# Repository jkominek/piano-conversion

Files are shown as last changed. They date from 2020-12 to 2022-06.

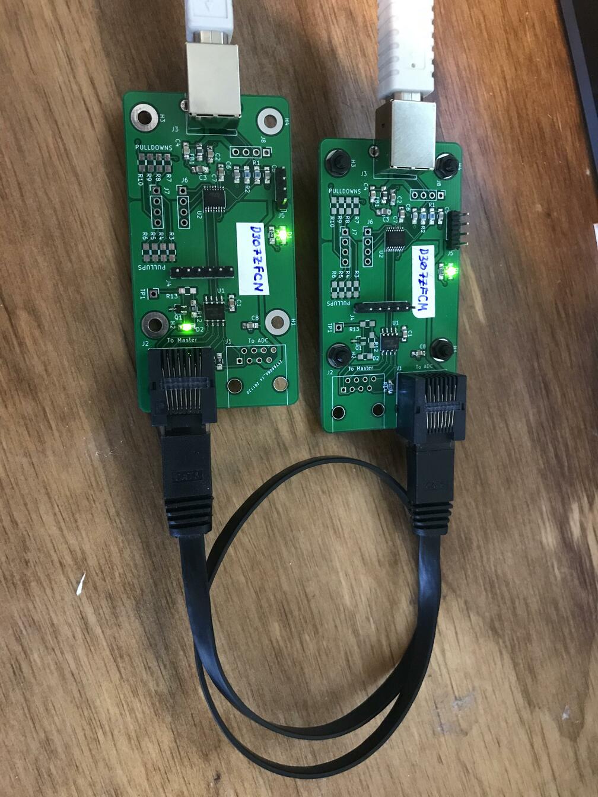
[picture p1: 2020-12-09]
images/link_adapters.jpg

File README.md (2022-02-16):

# About

This represents work on hardware/software for converting acoustic
pianos in to full featured MIDI controllers. The idea is to take
untunable pianos, or pianos whose restoration cost would wildly
exceed their value, and make something useful out of them.

See [the FAQ](https://github.com/jkominek/piano-conversion/wiki/FAQ)
to have common / likely questions answered.

Later work may expand that scope.

It was inspired by Evgeni Kumanov (CyberGene)'s "Cybrid" controller:
https://github.com/ekumanov/cybrid/

# Warning!

The hardware designs are unfinished. Some have not been fabricated.
Most have barely been tested, and there is not firmware to run a
completed system.

See the [Status page](https://github.com/jkominek/piano-conversion/wiki/Status) for where things stand.

# A Very Brief Overview

* hardware
  * Where most of the work has taken place. KiCad schematics and board
    layouts for the system.
* cubemx
  * STCubeMX files which correspond to the boards, the idea being that
    if you want to write your own firmware, you can start from here,
    and know that your pin assignments and such are all sane.
* firmware
  * Board firmware, some other stuff
* analyses
  * Data collected, and code/notes for processing it.
* mechanical
  * OpenSCAD files for physical parts which have been useful in
    construction of my prototype.

# More

See [DESIGN.md](https://github.com/jkominek/piano-conversion/blob/master/DESIGN.md) for system design information.

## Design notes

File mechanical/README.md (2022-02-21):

# Mechanical parts

Mechanical design is wholly outside the scope of this project.

There's too much variability in piano design, and personal aesthetics, for
a single mechanical design to be a productive goal.

But it can't hurt to put in some of the materials I've used. Most of them
will be OpenSCAD files, as the parts are simple, and OpenSCAD is available
to everyone. They might give you some ideas.

* odd_supports
  * Lets you make very complicated mounts to hold a dual slot 4040 extrusion up in the air at arbitrary angles, using two 2020 supports.
* cny70-protector
  * A plate to put over the CNY70 PCBs, which leaves the sensors exposed, while protecting them from direct hammer strikes.
* back-block & lr-block
  * Some simple blocks intended to mount onto single slot 4040 extrusions and hold the keybed from the side.
* mounting_plate
  * Adapter which holds my larger PCBs to the dual-slot 4040 extrusions.

More stuff will be forth coming.

# Sources of useful things

* Amazon is full of cheap hardware.
* McMaster-Carr, if you're not aware of it, will sell you just about every mechanical widget there is, for the right place.
* Misumi is my preferred supplier for aluminum extrusions. They'll cut and customize them for very reasonable prices, and are very precise.

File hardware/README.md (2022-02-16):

# What's in here

* adc-board
  * An STM32H743 reading 22 ADC channels and sending the results over RS485.
* led-power
  * Provides power to 8 strings of 22 CNY70 IR LEDs. Needs +48V. Optional I2C control.
* led-test-bar
  * For development only: little bar that holds a bunch of LEDs for testing the LED power board.
* link-adapter
  * For development only: allows a PC to connect to an ADC or main board.
* main-board
  * 8 ADC boards can plug in, their processed signals are managed
    by another STM32H743 and converted to MIDI in its various forms.
    Intended mainly for USB use, also has ethernet designed in.
    For all of the optional accessories, there are three I2C ports in
    the form of Qwiic connectors, for plugging in MIDI & pedal boards,
    and whatever other craziness you can conjure up.
* midi-board
  * An I2C to MIDI DIN board. Gets the extra UART, optos and DIN
    connectors off the main board so they're not taking up space if
    you don't need them.
* pedal-board
  * 4 1/4" TRS jacks for common MIDI keyboard pedals. STM32G0 for reading
    the signals and making them available to the main board via I2C.
* sensorboard-tester
  * For development/manufacture only, for testing/measuring sensorboards/CNY70s.
* sensorboards
  * Directory with a variety of board configurations for holding CNY70 sensors.

To put a sensor on every hammer and key of an 88 key piano, you would need:

* 176 sensor boards
* 8 ADC boards
* 1 main board
* 1 LED power board

Everything else is optional, but might make your life better.

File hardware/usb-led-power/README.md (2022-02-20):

This is a little USB-powered board which produces 4 constant current
outputs, each fixed to 20mA. Max voltage is 24V. With an LED Vf of
1.5V, that means you can drive <=16-ish LEDs off of each output. If
you drive just a single LED off an output, the constant current
limiter will be shedding 0.45W. It can probably handle that, but if
you want to use an output with fewer than 8 LEDs, consider putting a
resistor in series with them.  Remember V=IR. I is 20mA. Choose R to
eat 50-75% of whatever voltage will be left over after you subtract
the forward voltages of the LEDs from 24V.

The outputs inherit rather more noise from the USB power supply than I
would like. Which justifies much of the hassle I went through with the
design of the real LED power board. But if you don't like that one, or
want something for testing purposs, this might be helpful.

I don't generally suggest using it.

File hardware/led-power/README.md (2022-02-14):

# LED Power board

As covered in the main design doc, the board takes +48V, and uses them
to feed 8 strings of LEDs with a constant current of ~20mA.

# Design

See [the wiki page about the board](https://github.com/jkominek/piano-conversion/wiki/LED-Power-Board) for details on how it works.

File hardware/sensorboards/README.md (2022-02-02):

What do we have here?

* simple-1x
  * A single sensor board that tries to be generically useful
* 2040-centered-1x
  * A single sensor board that centers the sensor across the 40mm wide portion of a 20x40mm tslot aluminum extrusion.
* 2040-centered-2x
  * Same thing, but two sensors on one board.
* 2040-centered-4x
  * Same thing, but four sensors on one board.
* 2040-centered-4x-12deg
  * Same thing, but four sensors on one board and they're rotated 12 degrees, for bass hammers.
* 2020-offset-1x
  * A single sensor board that places the sensor to one side of a 20x20mm extrusion, and the connector on the other side.
* 2020-offset-2x
  * Same thing, but two sensors on one board.
* 2020-offset-4x
  * Same thing, but four sensors on one board.

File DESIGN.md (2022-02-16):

# Requirements / Goals

* Semiautomated calibration. Ideally once the hardware is correctly
  installed, it can be calibrated by playing all of the notes in
  order. It is expected this will require an attached PC running
  specialized software.
* It must be possible to make this work with just the extracted action
  of a grand piano. Mechanics are outside of the scope of what this
  project intends to worry about, but it would be ideal if a MIDI
  controller housing could be made for a piano's action, such that the
  action could be transferred between controller housing and piano
  with ease.
* Support for multiple common 1/4" TRS sustain pedals, or some other
  sensors that would be suitable for measuring the state of pedals
  still in their original state.
* The boards should be designed such that bad firmware can't wreck
  anything. I feel like this is important for open hardware type projects,
  where there is the possibility that folks might start fiddling
  with their firmware without a full understanding of the hardware.

### Distant future goals

* Integration with a Raspberry Pi 4 Compute Module capable of running
  Pianoteq so that a standalone piano can be produced.
* Alternatively, try to figure out how to get some open source synth
  software running on some sort of microcontroller, such that it can
  take MIDI over I2C and generate audio.
* Design/integration of DACs and audio amplifiers into that synth board,
  so that it can drive speakers directly.

# System Design

The hardware/software system is based around the Vishay
[CNY70](https://github.com/jkominek/piano-conversion/wiki/CNY70)
optical reflectance sensor. It consists of an infrared LED, and a
phototransistor sensitive to the LED, in a convenient package. It can
measure distances in the (roughly!) 0-10mm range.

In the full version of this conversion, 88 of those sensors would be
placed under the keys to detect note-off time & velocity, and 88 of them
placed at the end of the hammers' travel, so as to measure note-on timing
and velocity. This would prevent the "loud note" problem that troubles
some hybrid pianos. Additionally, information from the key sensors may be
used to signal to the synthesizer that the damper has been raised
(permitting resonsnace) before the hammer strikes. Sample based synths
could also use that information to preload samples.

(During the initial design of this I completely forgot that pianos usually
don't dampen the highest strings. If you want to leave the top 22 notes
undampened, you could eliminate one of the ADC boards. Or you could convert
a >88 key piano.)

### ADC Board

That's 176 sensors in a piano. 22 are monitored by each of these
boards.  The current through each one is converted to a voltage by a
transimpedance amplifier, and monitored by an ADC channel of an
[STM32H743](https://github.com/jkominek/piano-conversion/wiki/STM32H7).
Hopefully the STM32 will be able to process all 22 signals at between
10kHz and 20kHz. I expect to apply some digital low pass filtering.

Once the processor has determined that a note on, or off, is occurring
and measured the velocity, it is sent out over a RS485 serial
link. Use of RS485 should allow us to spread these boards out through
the structure of the controller, while maintaining relatively high
speed serial communications. The RS485 link takes place over two
twisted pairs of an ethernet cable. (NOTE we are NOT using ethernet,
just taking advantage of the large supply of high quality premade
cabling and jacks.) Having two twisted pairs permits full duplex
communication.

The same cable also carries ~5V power. Each board includes a single
switching regulator to bring the 5V down to 3.3V. The analog voltage
rails are produced by linear regulators, to reduce noise.

The board can be populated with optional components to make it into
a USB device. This isn't expected to be necessary, but may be more
convenient during the sensor calibration process. Two additional UARTs
are brought out to 0.100" header pins. Just in case.

Programming is performed over the JTAG header, intended for use with the
ST-Link/v2 programmer.

There is space for four LEDs, and a number of otherwise-unused pins are
brought out to sizable test points.

### Sensor board

Each sensor board will consist of nothing but some CNY70s, and a
0.100" header. 2*N pins will connect to the phototransistors, and come
back to the ADC board via twisted pair. The last two correspond to a
chain of all of the LEDs on the board.  The LEDs should be chained
together in rather long strings. Likely 22 sensors per string.

### LED power board

The LED power board is designed (as of rev3) to use an off the shelf
48V power supply, and provide a constant ~20mA to 8 different strings
of LEDs. Each string is intended to have 22 CNY70 LEDs on it.

We derive from the 48V a ~12V power rail for the rest of the analog
electronics on the board. The design as it stands should produce
constant currents which are extremely stable from time scales of a
year, down to 100kHz. The deterioration of the LEDs themselves is
expected to be the main source of change in the optical output.

Rev3 of the board adds a microcontroller which can monitor the LED
strings individually to detect errors, and also turn all the LEDs off
by shutting down the precision voltage reference.

### Main board

Intended to use a STM32H743 like the ADC board.

8 RS485 serial links, along with 5V distribution to the ADC boards.
Per-board high-side MOSFET control of power, so that boards
can be brought up in sequence once power has stabilized. Also allows
them to be power cycled in event of error, or to reflash them.

USB B device link, as the main/intended link to the host computer.

Four I2C controllers are brought out to three separate Qwiic headers,
so that a variety of common I/O devices can be attached without
requiring special development. (MIDI DIN, pedals, led power control,
RTC clock, ethernet/bluetooth, blinky RGB LEDs, etc)

Firmware is expected to process the fairly raw velocity messages
from the ADC boards, appyling any calibration, and sending them out
over any of the many MIDI links available to it (serial, USB, ethernet,
maybe even bluetooth).

#### Pedal board

A low powered STM32G0 a board with Qwiic headers, and 4 1/4"
TRS jacks for standard sustain pedals. 12 ADC channels go to
every pin of the TRS jacks in hopes that we can automatically
determine the behavior of the attached pdals.

#### MIDI board

Like the pedal board, the MIDI board is designed as a Qwiic device.
It also uses an STM32G0 to act as an I2C<->UART bridge, and has the
appropriate MIDI isolation circuitry.

### Link board

To facilitate development/testing of the ADC boards without the main
board, a "link board" has been designed. It is a full duplex RS485
board with power injection comparable to what the main board will
provide.

As an alternative to using the main board, a PC with enough link
boards to talk to all of the ADC boards simultaneously could skip out
on the use of a main board, in exchange for running more complicated
software locally.

# Construction/assembly requirements

See [the wiki Assembly Notes](https://github.com/jkominek/piano-conversion/wiki/Assembly-Notes)
for this info.

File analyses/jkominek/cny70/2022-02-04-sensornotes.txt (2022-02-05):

Put a CNY70 on a motorized stage, aimed at a white surface.
Moved it around, linearly, then at random, taking measurements
of the output. Phototransistor was fed into a TIA. High voltage
on the PT was 3.2584V. Reference voltage on the opamp was 1.9799V.
So there was 1.2749V across the phototransistor.

Voltages were measured with a EEVBlog 121GW multimeter.
Motion provided by a Creality Ender 3 V2.
Distances confirmed with Mitutoyo CD-6" ASX digital calipers.

poscommanded,posmeasured
5,4.66
10,9.66
15,14.66
20,19.57

All millimeters. Looks like the first column of the data needs -0.33
applied.  I think I was smashing the sensor into the target by 0.33mm.
Explains why it goes flat <=0.33

Maximum possible value for the raw data is ~1.9799V.

Gnuplot command for reasonable plot is

plot [0:] "2022-02-04-sensorlog.txt" using ($1-0.33):(1.9799-$2) with point

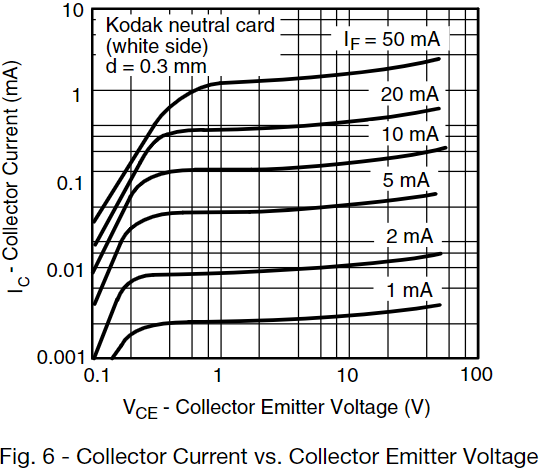
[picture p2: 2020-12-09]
images/ic_vs_vce.png

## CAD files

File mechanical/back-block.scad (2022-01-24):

rotate([180,0,0])
difference() {
  union() {
    cube([40, 50, 10]);
    translate([15, 0, -2]) {
      cube([10, 50, 2]);
    }
  }
  translate([20,10,-2.1]) {
    cylinder(h=14, d=5.2, $fn=32);
  }
  translate([20,40,-2.1]) {
    cylinder(h=14, d=5.2, $fn=32);
  }
}

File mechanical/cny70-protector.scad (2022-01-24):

xy = 7.5;
width = 9;
length = xy+(2.5+0.2)*2;
sensor_height = 5.6;
sensor_gap = 2;
// left to right, l_hammer_size > r_hammer_size
l_hammer_size = 33.5;
r_hammer_size = 33.3;
l_curvature = l_hammer_size / 2;
r_curvature = r_hammer_size / 2;

curvature_x0 = l_curvature;
curvature_m = (r_curvature - l_curvature) / 3;

module cny70_gap() {
  minkowski() {
    cube([xy, xy, (sensor_height+sensor_gap)*1.5]);  
    cylinder(h=0.1, r=0.2);
  }
}

module multiprotect(x) {
 imax = x-1;
 difference() {
   translate([0, -11.25, 0])
     cube([12.5*imax+xy,
           30,
           (sensor_height + sensor_gap)]);

   for(i=[0:imax]) {
      translate([i*12.5, 0, 0])
        #cny70_gap();
   }
   /*
   translate([0, xy/2, 0])
     for(i=[0:imax]) {
       curvature = curvature_x0 + curvature_m * i;
       translate([12.5*i, 0, curvature+sensor_height+sensor_gap])
         rotate([0, 90, 0])
           cylinder(h=12.5, r=curvature);
     }
   */
   translate([0, xy/2, 0])
     for(y=[-1:2:1]) {
       for(i=[0:(imax-1)]) {
         translate([10+12.5*i, y*-10, 2])
           cylinder(h=30, d=6.5, $fn=19);
         translate([10+12.5*i, y*-10, -2])
           cylinder(h=4, d=4.1, $fn=9);
       }
     }
  /*
  translate([0, -sensor_height/2, sensor_height/2])
    #sphere(r=2);
  */
 }
}

multiprotect(4);

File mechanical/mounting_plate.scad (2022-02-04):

x=1;

difference() {
    union() {
        minkowski() {
          translate([45, 0, 0])
            cube([25, 3*25.4, 5], center=true);
          cylinder(h=0.1, r=5);
        }
        for(y=[-1:2:1]) {
            translate([x*1.5*25.4, y*1.5*25.4, 0])
              cylinder(h=5, d=8);
        }
    }
    
    for(y=[-1:2:1]) {
        translate([x*1.5*25.4, y*1.5*25.4, 0])
          cylinder(h=20, d=3.5, center=true);
        
        translate([x*55, y*10, 0])
          cylinder(h=20, d=6, center=true);
    }
}

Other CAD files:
mechanical/lr-block.scad
mechanical/odd_supports.scad

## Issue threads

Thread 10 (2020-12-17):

LED Power Rev 1

jkominek, 2020-12-17:
Most of the fixes necessary for Rev 1 have been made and are covered under the [Board Revision Notes](https://github.com/jkominek/piano-conversion/wiki/Board-Revision-Notes).

- [x] Ferrite beads on the incoming power lines? The +15V and +48V are only used by linear devices, so the only HF noise will come from the supplies. We're not generating anything we should try to trap.
- [x] Final schematic/footprint/layout check.

jkominek, 2020-12-20:
78025ad didn't bother putting ferrites on here, The digital logic is optional, and even when present will only be used occasionally to check that the LED strings are still active. I did make the I2C address configurable, though. Jumpers or SMT resistors, as I did on all the other boards.

Closed 2020-12-20.

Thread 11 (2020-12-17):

Link adapter Rev 1

jkominek, 2020-12-17:
All the desired fixes/changes have been made. I don't anticipate bringing these up, they're just cheap enough they're worth getting in case I need more adapters; no sense building the old design.

- [x] Final schematic/footprint/layout check.

jkominek, 2020-12-20:
made some silkscreen improvements in 156ddb7. also improved a few net names making it easier to read the layout.

Closed 2020-12-20.

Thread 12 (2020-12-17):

MIDI board Rev 0

jkominek, 2020-12-17:
- [x] Might be able to drop one of the logic buffers, since we've moved the UART right onto the board. Check that. Want to keep the open collector inverter, as it means we don't have to configure the UART to invert bits or anything for us.
- [x] FInal schematic/footprint/layout check.

jkominek, 2020-12-18:
1d04dc2 removes the extra buffer, finishes the incomplete reset net, and tidies up some layout.

Closed 2020-12-18.

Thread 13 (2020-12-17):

Pedal board Rev 0

jkominek, 2020-12-17:
- [x] Final schematic/footprint/layout check.

jkominek, 2020-12-18:
fecdb71 splits the analog/digital power rails (more or less), and adds a second Qwiic header.

Closed 2020-12-18.

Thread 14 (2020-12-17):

LED Power Rev 1 bringup

jkominek, 2020-12-17:
- [x] Make sure the 5V regulator doesn't explode the MCP1501.
- [x] Check IO expander. Not necessary for a useful board.
- [x] Check I2C pass through performance?

jkominek, 2021-01-04:
IO expander can control the voltage reference, but reading back the status of the lines seems a little off. Probably because all the pins are floating. Will need to finish populating all of the resistors in the middle and check that again.

jkominek, 2021-01-05:
IO expander is fine. It occurs to me that it can check whether or not the individual lines are on, but it can't tell if the 15V and 48V are live. Should add some voltage dividers and hook those up to some more of the IO expander pins.

jkominek, 2021-01-05:
I2C passthrough seems fine

Closed 2021-01-05.

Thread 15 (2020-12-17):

ADC Board Rev 1 bringup

jkominek, 2020-12-17:
- [x] Check adjusted power supply filtration.
- [x] Check MCP120 chip.
- [x] Check 2V regulator.
- [x] Check transimpedance amplifiers.
- [x] Check JTAG header works right now.
- [x] Check RS485 wiring
- [x] Should put a microcontroller on to ensure that some of the rearranged digital lines are ok (the UART in particular)

We'll want the new TIA circuits for testing/writing analog processing code going forward.

jkominek, 2021-01-06:
Hmm not sure what I meant by "adjusted power supply filtration". Using surface mount caps? Guess I can compare old & new +3.3V lines on the scope.

jkominek, 2021-01-13:
+5V and +3.3V looked pristine when I was checking the MCP120 at power-on. Calling that good enough.

jkominek, 2021-01-14:
UART3 to RS485 works fine.

Closed 2021-01-14.

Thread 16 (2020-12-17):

Minor boards

jkominek, 2020-12-17:
- [x] Sensorboard, final schematic/footprint/layout check.
- [x] Sensorboard tester, final schematic/footprint/layout check.
- [x] LED test bar, final schematic/footprint/layout check.

jkominek, 2020-12-18:
LED test bar: Added copper pours for the lowest voltage net on the board, some corresponding large exposed pads for clipping onto, and silk screen for them.

jkominek, 2020-12-20:
bfe854e Sensorboard: finally looked at the gerber files for the Cybrid sensor, and better matched their dimensions. Got the width down to 9mm, and moved the sensor 10mm from the mounting hole center. I wouldn't be surprised if different pianos end up needing a variety of different boards, (Including ideally some boards that hold multiple sensors.) But this should serve as a better starting place.

jkominek, 2020-12-20:
6f696a1 Sensorboard tester: while working on the sensorboard, realized that the header on it might need to be installed backwards, to ensure clearance for hammers striking the sensor, or whatever. So I added mirrored female receptacles on the tester board, to allow for plugging in reversed sensorboards.

Closed 2020-12-20.

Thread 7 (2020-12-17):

ADC Board Rev 0 bring up

jkominek, 2020-12-17:
There are three bring up issues to check before the Rev 1 schematic can be finalized:

- [x] Test that the USART/RS485 transceiver work correctly. It _should_ be fine, as I used the same symbol/footprint as the link adapter board, and USARTs are simple, but... who knows.
- [x] Test that the 22 channels of near-simultaneous ADC conversion works. I should really have done this sooner, as the project relies heavily on this working.
- [x] See if the built-in bootloader works on initial power up. The ST app note on the bootloader has some ominous warnings about V9 of the bootloader, which is the most recent, and presumably what I've got on my parts.
- [x] Slightly easier, see if it works on the USART pins we're currently using. Moving to a different USART probably isn't a problem, but why mess with a layout that seems ok.

jkominek, 2020-12-17:
Z/Y pins on the RS485 transceiver were swapped. Schematic and layout have been fixed (not yet committed).

jkominek, 2020-12-18:
Bootloader seems to be responsive on USART3 immediately after power on, no shenanigans required. I'm not quite getting it to do what I want, but "responsive" is all I can hope for from a hardware standpoint. c76639c swaps USART1 and USART3 on the RS485 transceiver.

jkominek, 2020-12-20:
22 channels of ADC conversion at 15kHz seems to work ok. Not sure about the conversion noise, but I'm pretty sure there is a lot of room for tweaking once I'm taking data off of real sensors watching real hammers/keys. So... design looks workable!

Closed 2020-12-20.

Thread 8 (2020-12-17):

ADC Board Rev 1

jkominek, 2020-12-17:
Most of the fixes necessary for Rev 1 have been made and are covered under the [Board Revision Notes](https://github.com/jkominek/piano-conversion/wiki/Board-Revision-Notes).

- [x] Completion of #7
- [x] Bring out MCO1 and MCO2 on some test points, or at least confirm that the existing test points expose some timer pins. Goal is to make it convenient to measure the frequency stability of the built-in oscillators,
- [x] Triple check the transimpedance amplifier design in the analog half. @DigitalExegete agreed to help. :)
- [x] Final symbol/footprint/layout checks.

jkominek, 2020-12-20:
Past me was a genius, MCO1 and MCO2 are already available on test points. The same pins (PA8/TP26, PC9/TP25) also have some timer outputs on them.

jkominek, 2020-12-21:
c9634bf tweaked the edges of some of the copper pours around the analog area, and adjusted the routing on the NRST line.

jkominek, 2020-12-21:
been staring at the TIA forever. pretty sure we're good to go.

Closed 2020-12-21.

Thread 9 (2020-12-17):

Main Board Rev 0

jkominek, 2020-12-17:
Subtasks:

- [x] Triple check the high-side power control of ADC boards.
- [x] Include a SPI memory part, EEPROM or FLASH, or something. Find a common footprint, we can worry about what size memory (or even if we'll use it) later.
- [x] Double check the UART pin assignments, make sure we don't have an RS485 transceiver hooked up to something that isn't a UART.
- [x] Final symbol/footprint/layout check. Don't forget ERC/DRC.

jkominek, 2020-12-21:
63abe29 Fixes a UART pin error, _and_ an I2C pin error. Sigh.

jkominek, 2020-12-21:
0f9a079 includes an SPI flash using a common footprint for a SPI memory.

jkominek, 2020-12-21:
5072ae0 Must've been in a hurry when I did the power control. Had the p-channel FETs backwards. And an extra resistor on each one that I can't, for the life of me, figure out why I wanted. FETs flipped, resistor removed, and package layout made pleasingly symmetric.

jkominek, 2020-12-21:
016cd60 ran ERC/DRC, removed some unused nets and marked the pins NC. (leftovers from when I thought the pedal inputs might come to this board directly.)

jkominek, 2020-12-21:
Pretty sure we're all done with this. 3a703c3 moved the ethernet LEDs to a single 2x3 header. A 1x3 is still used for boot selection, but I'd expect most users to jumper that. I'm expecting this will need another rev, so I'll worry about putting in pads to allow it to be set during surface mount assembly in that rev.

Closed 2020-12-21.

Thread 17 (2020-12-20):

Update PCB layouts with new revision number & generate gerber files

jkominek, 2020-12-20:
I update the board revision number right before producing gerber files. So this will be the very last thing to do on the milestone.

- [x] Commit updated silkscreen for all boards

Generate gerber files for the following, and attach to the release:

- [x] Main board
- [x] ADC board
- [x] LED power
- [x] LED test
- [x] Sensor board
- [x] Sensor test
- [x] Pedal
- [x] MIDI
- [x] Link adapter

jkominek, 2020-12-22:
gerber zips generated, and attached to release.

Closed 2020-12-22.

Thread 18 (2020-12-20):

Main board rev 0 bringup

jkominek, 2020-12-20:
- [ ] ~~Qwiic header pass-through~~ Every one on the main board is its own bus, this item must've predated that change.
- [x] Power input, reverse polarity protection & regulation
- [x] Control of N/P channel MOSFET array
- [x] 20MHz ~~& 25MHz~~ oscillators
- [x] One stack of RS485 transceiver & jacks, to confirm correct wiring (sigh)
- [x] Microcontroller (UARTs & I2C primarily)
- [ ] ~~Ethernet chip, magjack, and microcontroller use of ethernet~~ Going to move networking onto an optional board.

jkominek, 2021-01-03:
tempted to move the ethernet off this board in the next rev, in which case i probably wouldn't bother to bring it up on here.

jkominek, 2021-01-09:
JTAG works and the STM32 is still live after my hand soldering. I'll have to cobble together some firmware to test the UART and I2C.

jkominek, 2021-01-14:
brought the stcubemx project definition up to date. should be good to generate a basic project and start poking things.

jkominek, 2021-01-15:
USB D+/D- are swapped.

jkominek, 2021-01-15:
UART4 and USB are fine.

jkominek, 2021-01-15:
and I2C4 works, so we're all set i think.

Closed 2021-01-15.

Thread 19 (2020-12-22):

Pedal board Rev0 bringup

jkominek, 2020-12-22:
- [x] Assembly
- [x] Check that the ADS7830 works
- [ ] Check it with a pedal

jkominek, 2021-01-20:
didn't really get the pedal pinout right enough to be worth trying it with a pedal. ehhh.

Closed 2021-01-20.

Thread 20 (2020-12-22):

MIDI Board Rev0 bring up

jkominek, 2020-12-22:
- [x] Assembly
- [x] Check MIDI out circuitry
- [x] Check MIDI in circuitry
- [x] Check the SC16IS741

jkominek, 2021-01-02:
UART is functional. rev0 appears to have no errors that prevent its use.

Closed 2021-01-02.

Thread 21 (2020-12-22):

Check BOM against JLCPCB SMT parts list.

jkominek, 2020-12-22:
JLCPCB being one of the easier (and still reasonably priced) ways for the average person to get a board assembled, I'm trying to keep the parts used to things that are available via JLCPCB.

- [ ] Compile total BOM
- [ ] Check that JLCPCB has an appropriate corresponding part
- [ ] Document correspondence
- [ ] Build up BOM spreadsheets or something for use with JLCPCB? Haven't had them assemble anything, not sure how that works.

jkominek, 2021-01-13:
I went looking through JLCPCB's basic parts library for FETs for the main board. Looks like the relevant options are all SOT-23-3, so I'll need to tweak that for rev 1.

Here are SOT-23-3 FETs, and after brief inspection, the most likely candidates are marked with *

N-channel FETs: C8545(*), C20917
P-channel FETs: C10487, C15127(*), C8492

davidedelvento, 2021-11-10:
Hi @jkominek have you made any progress on this? And also with the CPL files? I would like to start ordering some boards, but I see only gerber files in https://github.com/jkominek/piano-conversion/releases so I'm not sure how to ask jlcpcb to do the SMT assembly without them.

jkominek, 2022-01-09:
No progress on this. I'm not sure it would even be useful at this point, with the widespread parts shortages. I was expecting to have to change some parts in order to make the board JLCPCB-assemble-able, which is fine, but doing it right now seems like an exercise in frustration.

jkominek, 2022-02-07:
I have started looking things up, in hopes of replacing some parts with ones which are more available / have more drop-in replacements, and also just assessing the situation. I used fewer distinct parts than I remembered!

https://github.com/jkominek/piano-conversion/wiki/Parts-Compatibility

So far it looks like the only totally unavailable parts are the microcontrollers, and the USB ESD protector. If there isn't anything else broadly available with a matching footprint, I'll talk to a real EE and design in something more generic.

davidedelvento, 2022-12-30:
> Compile total BOM. The first pass of this should probably ignore resistor values,
> the ones in the schematics are very hand-wavy and don't strictly match what I've used.

Is this still the case? I see most resistor values are populated in the ADC board and they seem okay to me. Instead there are a number of missing capacitor values (some of which in the PCB appear to be connected nowhere, which probably should be a separate issues?)

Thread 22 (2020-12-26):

ADC Board Rev 2

jkominek, 2020-12-26:
Place to record necessary changes for rev 2 of the board:

### Necessary changes

- [x] Bring the JTAG header in 1-2mm from the edge of the board, so that the pcb stickvise can grab the board even with that header attached.
- [x] Silkscreen for +5V and GND on the external power header

### Noncritical changes

- [x] Increase thermal relief on pin 3 of the MCP120, to ease hand soldering.
- [x] Consider just increasing the thermal relief everywhere, to ease hand soldering.
- [x] Move the power LED further away from the 8p8c jack, to ease viewing.
- [x] Bump up the size of the electrolytic cap footprints by 1, to better match the cap selection you get in variety packs.

### Possible improvements

- [ ] Consider swapping the location of the RS485/power input and the USB connector. As it is, the +5V power to the analog linear regulator is passing under the MCU, which will act as a source of noise.
- [x] I realized that I was probably wrong about the suitability of replacing the voltage reference with a simple linear regulator. I can probably do an error analysis to determine how any noise on the regulator will be converted into ADC errors. I should probably do so as penance for my overeager substitution.
- [x] The MIC5366-2.0YC5 linear regulator data sheet only calls for 1uF caps on input and output; the schematic lists 2.2uF. That's probably fine. Should definitely keep it in mind, though, and consider it as a spot for BOM reduction.

jkominek, 2021-01-17:
First batch of changes made in f3f059a

jkominek, 2021-01-18:
832f42c Restored the MCP1501 for the analog reference. Error analysis said that for a fixed Vref (2.5, 2.048, etc), the noise on Vref was passed through linearly to the output. Not surprising. Increasing Vref also reduced the noise, but bumping up to 2.5V doesn't seem worth it for the reduction in linearity that would likely cause in the CNY70's phototransistor output.

I'm going to pass on rearranging the connections in this rev.

Closed 2021-01-18.

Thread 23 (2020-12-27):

Main board rev 1

jkominek, 2020-12-27:
Place to record necessary changes for rev 1 of the board:

### Important

- [x] MicroSD card slot.
- [x] RS485 transceiver SO8 footprint appears to be wrong; awkwardly wide and difficult to solder.
- [x] Compress the board to <= 100x100mm.
- [x] Remove all ethernet
- [x] Expose a couple of carefully chosen GPIO to act as ~IRQ pins for external Qwiic boards. Bring them out on headers, kind of like the switches/LEDs/etc.
- [x] Change the FET footprints to SOT-23-3 to accomodate JLCPCB SMT basic parts library.
- [x] Swap USB D+/D- into the correct positions.

### Noncritical issue

- [x] Scoot the +5V and GND silkscreen slightly further away from the power connector.
- [x] Add silkscreen to put the JLCPCB part number under a stack of RJ45 jacks.
- [x] The Qwiic headers will be hard to hand solder. Giving them some more space sort of contradicts the plan to narrow the board, but anything we can accomplish will help.
- [x] Increase the space between the 3.3V regulator, and the power/reset/status header, to ease rework.
- [x] Bump up the size of the electrolytic cap footprints by 1, to better match the cap selection you get in variety packs.

jkominek, 2021-01-16:
First batch of changes made in b8bb4f2. It was basically a complete relayout. I stripped all the traces, repositioned everything, and then reconnected it all.

* RS485 transceiver footprint fixed
* Compressed board to 100x100mm exactly
* Removed ethernet
* Changed FET footprints to SOT-23
* Swapped USB D+/D- to correct positions
* Spaced out +5V and GND silkscreen on power input
* Added JLCPCB order number silkscreen
* Spaced out Qwiic headers
* Added some more space around 3.3V regulator.
* Slightly increased size of electrolytic caps.

jkominek, 2021-01-16:
2efb067 finishes off the changes.

Closed 2021-01-16.

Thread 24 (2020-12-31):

MIDI Board Rev 1

jkominek, 2020-12-31:
- [x] Ensure that the 40mm spaced mounting holes have a setback from the board edge consistent with our other panel-mount boards. Ensure there is enough space around them for whatever mechanical solution will hold them to the panel.

### BOM-only

- [x] The 74LVC1G06 should be a 74LVC1G07, so that the MIDI OUT side works.

### Non-critical issues:

- [x] Bring out the pair of ~IRQ & GND on a little header. Maybe a pair of them so they can be daisy chained.
- [x] Increase the space between the Qwiic connectors, to facilitate hand soldering
- [x] Add a two-pin header for power, to ease testing
- [x] If we stick with the TLP185(SE add some silkscreen to make orientation more obvious.
- [x] Update the TLP185(SE footprint to remove the unused pins in the middle.
- [x] Bring the I2C bus out to a 0.100" header.

jkominek, 2021-01-19:
Changes made in 320dd0f.

Closed 2021-01-19.

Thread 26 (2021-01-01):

Pedal Board Rev 1

jkominek, 2021-01-01:
- [x] Rev0 is huuuge. It can be made narrower. Maybe?
- [x] Push the TRS jacks back slightly, so the mounting flange on the face of the jack lines up with the PCB. Some quick measurements suggest that "slightly" is 2.1 to 2.3mm in this case.
- [x] Ensure that the 40mm spaced mounting holes have a setback from the board edge consistent with our other panel-mount boards. Ensure there is enough space around them for whatever mechanical solution will hold them to the panel.
- [x] The TRS jack footprint has an error, in that what should be the silkscreen outline is actually a line on the solder mask exclusion layer. So what initially appears to be a nice outline is actually exposed (and HASL'd) copper.

### Noncritical

- [x] Bring the I2C bus out to a 0.100" header.

jkominek, 2021-01-20:
Changes made in bbeeac4
- Made it narrower, but had to expand the space between mounting holes.
- Moved the jacks back 2.3mm.
- 10mm to board edge, 5mm clearance on the inside of the board, 7.5mm clearance on either side
- Fixed the outline to be silkscreen, not a hole in the mask
- Added I2C bus header
- Made nice little three pad footprints for spots where you need a pull up or a pull down.
- Drastically increased the space between the Qwiic headers
- On the pedal jacks, the signal is really on the Tip, not the ring where I had it. Not sure what I was thinking.

Closed 2021-01-20.

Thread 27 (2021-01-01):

LED Power board Rev 2

jkominek, 2021-01-01:
- [x] Vref net requires a pulldown (2.4k seems to be working fine) in order to drain the charge to 0V when the MCP1501 is shut down by the MCP23017. Without it, Vref basically floats, and the the constant current goes undefined.
- [x] Voltage dividers on +15V and +48V to turn them into inputs for the IO expander, so it can check that the supplies are working.

### Noncritical

- [x] Increase the space between the Qwiic connectors to ease hand soldering.
- [x] Bring the I2C bus out to a 0.100" header.
- [x] Still need more space between the individual string screw terminals/headers and their corresponding indicator LEDs. It should be sufficient to bring them in towards the middle by 0.5mm, which should roughly line them up with the courtyard of the mosfets.

jkominek, 2021-01-17:
Made all these changes in cfa9cb8. Also converted the board to four layers, to avoid the hassle of routing +15V and +48V everywhere.

Closed 2021-01-17.

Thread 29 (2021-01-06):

Networking board Rev 0

jkominek, 2021-01-06:
Putting ethernet on the main board is an unnecessary complication, which increases the board size/BOM/cost/etc. Many users probably won't even want it. It's certainly non-existent on every other digital piano, so it shouldn't have such a prominent place.

I decided I2C was a nice idea after I'd already started putting the ethernet onto the main board, and didn't reevaluate its suitability. Doing full TCP/IP over I2C would probably be a pain, but the main board doesn't need to. It can mostly just worry about MIDI and its own configuration.

So we'll move all networking off to another board, and pick up WiFi at the same time. The networking board will feature an ESP32 module, acting as an I2C slave to the main board. The ESP32 will bring along WiFi, and we'll add a SPI-based Microchip ENC28J60 to get 10Mbps ethernet. The only thing that will need to move across I2C is MIDI messages (and maybe some sysex for configuration/control, but that's minor). All of the TCP/IP and RTP MIDI stack stuff can be handled on the ESP32, where it won't bother the realtime stuff happening on the main board.

### Concept Verification Tasks

- [ ] Check ENC28J60 board with a Bus Pirate
- [ ] Check ENC28J60 board with an ESP32 module
- [ ] Reverse engineer the now-known working ENC28J60 board.

### Circuit/Layout Tasks

- [ ] +5V power input circuitry. The ESP32 draw is expected to exceed what we'll want to provide over the I2C cabling
- [ ] Get an ESP32 on a board, as an I2C slave.
- [ ] Qwiic header(s). ESP32 as slave, and ESP32 as master, so it can have some devices of its own. (Or be attached to one of the buses that the main board is also mastering, for a multimaster type thing.)
- [ ] Add ENC28J60 as SPI slave to the ESP32

jkominek, 2021-01-08:
Looks like Espressif's ESP32-ETHERNET-KIT-VE‎ might be sufficient with just some extra wiring.

I'll need to read the specs fully, but if it'll work, this board might be dropped or lowered in priority.

jkominek, 2022-02-14:
Haven't gotten around to playing with the Espressif board, but I did pick one up. Going to consider this dead, at this point I'd sooner find something that worked for the job than design an ethernet circuit myself.

Closed 2022-02-14.

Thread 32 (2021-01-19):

Update PCB layouts with new revision number & generate gerber files

jkominek, 2021-01-19:
I update the board revision number right before producing gerber files. So this will be the very last thing to do on the milestone.

- [x] Commit updated silkscreen for all boards

Generate gerber files for the following, and attach to the release:

- [x] Main board rev1
- [x] ADC board rev2
- [x] LED power rev1
- [x] Sensor test rev1
- [x] Pedal rev1
- [x] MIDI rev1

jkominek, 2021-01-22:
Tagged 91fbc96 as rev20210121

Closed 2021-01-22.

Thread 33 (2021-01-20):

Main board add RTC oscillator, battery header and appropriate Vbat circuitry

jkominek, 2021-01-20:
I'd like the ability to run the RTC on the main board, accurately. That'll let us track calendar time, so that we can properly time stamp files stored on the SD card.

Why do we want to time stamp files on the SD card? I'd like to be able to record everything played into MIDI files on the SD card, to duplicate the Pianoteq feature of remembering everything that's played. It's not a super high important feature, but it should be possible to at least squeeze the relevant stuff onto the PCB (with no downsides) even if it isn't populated.

See section 2.1.3 of AN4938. It looks like the STM32H743 can charge the battery a little bit? Do I need to put something in place to handle the possibility of a missing battery? Maybe a diode with a 1.5V drop from Vdd to Vbat? Or just some spot to solder a resistor between Vdd and Vbat?

So we need:

- [x] 32.768kHz oscillator, reasonable accuracy
- [x] Battery header. Polarized two-pin JST thing compatible with batteries like https://www.sparkfun.com/products/13852

davidedelvento, 2021-01-20:
That is a great feature to have!

jkominek, 2021-01-21:
Added in 2a38bf9

Closed 2021-01-21.

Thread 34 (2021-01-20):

Toy/barebones synthesizer + audio output module

jkominek, 2021-01-20:
A sort of pie-in-the-sky idea, that isn't part of any milestone, or blocking anything:

A board, conforming to the overall I2C/Qwiic scheme, which presents itself like the I2C UART on the MIDI output board, basically taking a stream of MIDI data written to register 0x00. But instead of streaming that MIDI data elsewhere, it runs it through a simple synth, generating an analog signal, and feeding it to any of line outs, headphone amps, or power amps for real speakers.

I don't have any interest in trying to implement even a sample-based piano synth in hardware, let alone a fancier synth than that. But some simple 32 voice sine wave + some harmonics that responds to note on velocities, note off, and sustain pedal could maybe be useful? I'm imagining a situation where you've taken a unit to a tech for them to work on the regulation of the system after confirming that whatever your issue is, is present even when using this simple synth.

It would also serve as a reference for anyone who wanted to build a more advanced synth. For instance, it is possible to get a Raspberry Pi to act as an I2C slave device. So, you could make a board that brings in the Qwiic connection, has plugs for a Raspberry Pi compute module (both for it to mount, and so you can put a display/keyboard/mouse on it), takes the audio output from the module, runs it through amps. Then you could slap Pianoteq on the Pi module, and have a largely standalone system with "real" synthesis and "real" audio.

davidedelvento, 2021-01-20:
I think this is a fantastic idea, for even much more than you say. For example, my NU1 I does not have any "long lasting" organ-like sound. Every sound it has is a piano-like decaying one. It's a big hassle to do slow harmony exercises in that setup, because the sound disappears earlier than I need it. Even a simple sine-wave would be very useful for that (assuming it can handle polyphony, 16 notes suffice for the purpose). A possible problem which I have with phone apps that I use to workaround the problem is with the lowest or highest frequencies, which become gradually inaudible, likely because of the phone line-out amplification. The problem might be worse at low frequencies if you go with sine waves without many harmonics (which is a problem on acoustic pianos too). I suspect the setup you describe having similar problems?

It would be phenomenal (but probably too much?) if you can somewhat have a small number of programmable voices, even if just in firmware (rather than in a user interface). For example each voice could have a number of harmonics AND the attack-decay-sustain-release envelope, and maybe even temperament/tuning, and maybe the harmonics are different in different registers (low vs high notes). But that is probably too much and could quickly skyrocket to full-blown synth... which you rightly do not want to spend your time one -- so likely best to be left to the external R-Pi. Unless... the reason I mention is that I don't know what would be easy/possible on the hardware you have in mind. If hardware would easily support this kind of things, but the problem is just firmware/software, I'll be happy to take a look and see what it takes to make it, and perhaps contribute.

Last, why would one want to use the R-Pi as an I2C slave device rather than connecting to this piano controller via regular MIDI-over-USB? To be clear: this is a sincere question, not a rhetorical one: I don't know the answer and/or the advantage of one vs the other solution.

jkominek, 2021-01-21:
> I think this is a fantastic idea, for even much more than you say. For example, my NU1 I does not have any "long lasting" organ-like sound. Every sound it has is a piano-like decaying one. It's a big hassle to do slow harmony exercises in that setup, because the sound disappears earlier than I need it. Even a simple sine-wave would be very useful for that (assuming it can handle polyphony, 16 notes suffice for the purpose).

What, don't you like Organteq? 🤪

> A possible problem which I have with phone apps that I use to workaround the problem is with the lowest or highest frequencies, which become gradually inaudible, likely because of the phone line-out amplification. The problem might be worse at low frequencies if you go with sine waves without many harmonics (which is a problem on acoustic pianos too). I suspect the setup you describe having similar problems?

I've not designed an audio amplifier before, but I feel like you'd simply run into problems with your speakers before the amplifier. Subwoofers and such only go so low. Pianos and organs being physical large objects just have an advantage with producing low frequencies.

Adding a line-level output that's a low-passed version of the signal, so that you've got something to route to your subwoofer is probably the only thing that's within the scope of this project.

> Unless... the reason I mention is that I don't know what would be easy/possible on the hardware you have in mind. If hardware would easily support this kind of things, but the problem is just firmware/software, I'll be happy to take a look and see what it takes to make it, and perhaps contribute.

I don't have any particular hardware in mind at the moment. I could probably squeeze a 16-32 voice synth with ADSR and a few harmonics onto another one of the STM32H743s I'm already using without trying very hard. The code would of course be open like everything else, so once you got a development environment up, you could easily sit there reflashing the part, and immediately hitting keys to hear what it sounds like.

Using something more DSP-oriented would probably broaden the options available. Before I actually go anywhere with this I'll look around, there have to be some other open source MIDI synths. If any of them look good I'll just lift whatever they're doing and put the interfaces on it that I want. 😃

> Last, why would one want to use the R-Pi as an I2C slave device rather than connecting to this piano controller via regular MIDI-over-USB? To be clear: this is a sincere question, not a rhetorical one: I don't know the answer and/or the advantage of one vs the other solution.

Oh, hah, yes. My plan every other time I thought about this was to use USB, as you describe. I just forgot that USB was even an option when I was coming at it from the stand point of incrementally improving a toy synth board into something "real".

That said, there might be less latency (🤪) if the Pi was driven by the rest of the system. USB has to poll devices, and the USB stack has a lot more stuff in it... I'm not sure. It might be amusing to look at.

davidedelvento, 2021-01-21:
> What, don't you like Organteq? :zany_face:

Actually I love Organteq! In my opinion is so much closer to a real organ than Pianoteq is to a real piano. My only problem is that I'd use it so little that I can't justify its price. I'd happily have bought it if it had the same Pianoteq price structure or if it came at a discount if bought with Pianoteq too... or at its current price it included some hardware preconfigured and optimized to run it on (I know it _should_ work on R-Pi, but as I said I need it only for some exercises, so I have zero interest of spending lots of money **AND** lots of time on it)

> Using something more DSP-oriented would probably broaden the options available.

My experience with them is 20y old so I'd better keep my mouth shut in this regard :)

> Before I actually go anywhere with this I'll look around, there have to be some other open source MIDI synths.
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
jkominek, 2022-02-16:
Leaving some relevant-looking links here:

- https://hackaday.io/project/9538-stm32f746g-discovery-sf2-midi-synth
- Older version of fluidsynth stripped down for microcontrollers: https://github.com/julbouln/lfluidsynth
- https://github.com/julbouln/stm32f7discovery_midi_synth
- https://github.com/julbouln/musicboard

davidedelvento, 2022-02-17:
> https://github.com/julbouln/musicboard

If my understanding is correct this provides almost everything, the only missing piece is that the audio out is USB only rather than signal, but that should be easily added from the DAC. It claims it needs lightweight resources, so... Would you deploy it on a dedicated board as in your initial comment, or do you have enough spare computing power on some other board? And also, fluidsynth is so feature rich that raises the question of what sort of UI should one utilize to control it? I think that would open the can of worms of button/LED vs display vs use-your-smartphone.... Do you want to go there? I guess you can answer: no just use one sound as configured last time you connected it to a computer or smartphone... Phone? Wait, if you have the phone in your pocket (who doesn't), there's even a phone version of fluidsynth which works pretty well, I've used it often. And that is why I stopped looking at the STM32 port after the first difficulty: you can just hook up the phone to the MIDI-over-USB of the piano-conversion and you have the MIDI, the synth, plenty of room for samples, the DAC, the amplifier, a speaker (ahem), a headphone amplifier and its corresponding jack... Possibility to record MIDI and/or audio, connect to the internet to send the data somewhere else... Hard to justify efforts to develop solutions (and money if a separate board needs to be added to the BOM) just to compete with all of that these days....

If anything, I'd make a MIDI-SysEx-base myTechnician to access settings, and a corresponding desktop and mobile app (similar in concept to what I proof-of-concept'ed [here](https://github.com/davidedelvento/Mybrid/blob/main/MyTechnician/mytechnician/__init__.py)) - but I digress, that should be a separate discussion

jkominek, 2022-02-17:
To be clear, I'm mostly just leaving notes here for completeness' sake. I don't currently intend to do any work on this task. Happy to discuss it, and provide guidance if somebody comes along and thinks it sounds like fun. But that'll be it.

> If my understanding is correct this provides almost everything, the only missing piece is that the audio out is USB only rather than signal, but that should be easily added from the DAC.

Looks like the musicboard project (the more recent of the materials) has analog output through an external DAC (the "CODEC"), which is what I'd do, because it's what I've seen in all the schematics for professional products. :) Also it is really easy.

> It claims it needs lightweight resources, so... Would you deploy it on a dedicated board as in your initial comment, or do you have enough spare computing power on some other board?

However light it is, I don't intend to add any audio processing to the main board, which is where it would have to reside. (I'm actively stripping everything I possibly can off of the main board, and feeling pleased with myself for my success.) I expect to have it broadcast MIDI over one or more I2C buses, to be picked up by whatever else. Could be a hypothetical synth board; far more likely to be the MIDI DIN board or ethernet/bluetooth adapter.

> And also, fluidsynth is so feature rich that raises the question of what sort of UI should one utilize to control it?

To whoever implements this: I expect to have non-MIDI USB endpoints available for talking to the main board from a PC, over which you could command it to send arbitrary stuff via I2C.

> Do you want to go there?

I'm not going anywhere near this. :)

> you can just hook up the phone to the MIDI-over-USB of the piano-conversion and you have the MIDI, the synth, plenty of room for samples, the DAC, the amplifier, a speaker (ahem), a headphone amplifier and its corresponding jack...

Yup, and I've got a USB-to-lighting cable around some place and Ravenscroft on my phone so that I can test that this works.

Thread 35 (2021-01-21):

Main board rev 1 bringup

jkominek, 2021-01-21:
- [ ] MicroSD card
- [ ] RTC
- [ ] ~IRQ pins
- [ ] Check USB correct this time

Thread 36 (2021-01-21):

ADC Board rev 2 bringup

jkominek, 2021-01-21:
- [x] JTAG header spacing
- [x] Check that the returned voltage reference works

jkominek, 2021-03-18:
I should note that the thermal relief on all the joints I assembled was nice; nothing really took an unreasonable amount of time to solder.

Closed 2021-03-14.

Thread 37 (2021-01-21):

LED power rev 2 bringup

jkominek, 2021-01-21:
Check:

- [ ] All spacings
- [ ] ~IRQ header
- [ ] Voltage dividers as IO inputs
- [ ] Vref pulldown

jkominek, 2021-03-14:
Board is assembled; need to actually check these things.

jkominek, 2022-02-14:
Spacings were good enough and Vref pulldown doesn't seem to have broken anything. The other issues were MCP23017-related, and the next rev doesn't use that. So, all done here.

Closed 2022-02-14.

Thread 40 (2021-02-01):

Pedal Board Rev 2

jkominek, 2021-02-01:
- [x] The TRS tips, which goes to the ADC inputs, have a series resistors on them, but we should add some caps to those signals, near the connector. This will help clean up the signal, and add ESD protection. 10 ohm series + 1uF should be a ~15kHz cutoff frequency, which is still higher frequency than necessary, but should help reduce aliasing, and keeps the cap size reasonable.
- [x] Convert to use of an STM32G0
- [x] We can add support for IRQ lines, now that there will be a tiny uC to detect changes. Add the header, and insert the transistor necessary to perform the pull downs.
- [x] Connect every single TRS signal (3 pins, 4 connectors) to a different ADC input on the STM32. By converting some of the pins on every connector to outputs and applying 0s and 1s appropriately, we can supply the power for the potentiometer in the pedal to work. Then the ADC can read the remaining pin per connector, and use that result.
  * more of a firmware issue, but start thinking now, what's the algorithm to automatically determine the pedal's configuration?
- [x] Bring out at least four of the ADC lines on header pins, along with VCC and GND, to facilitate connections to a broader range of sensors. Possibly all of the ADC lines.

davidedelvento, 2022-02-16:
Perhaps add space for other kind of connectors as inputs, in addition to the TRS for external pedals. Some people might want to use a "regular" sensorboard to measure movements of something attached to salvaged acoustic pedals. The range of interesting movement for una corda, sostenuto and dampers is not very different from the hammers, so I'd expect three 1x boards working well for this use case, if this board is able to support them. No need for the more fancy stuff that you do for the hammers, IMHO.

jkominek, 2022-02-16:
Hmm, I'd imagined attaching mechanical pots to such things... somehow, and then cables with TRS plugs. The other thought I'd had was encoders, either mechanical or magnetic, which wouldn't work with this design.

But somebody using optical reflectance is also reasonable. https://www.sparkfun.com/products/15334 would cover the simple case, with appropriate firmware support on the main board. There wouldn't the same smarts that this version has.

I'll think about making an alternative "simple sensor board", which would have space for the same STM32G0, appropriate I2C ports, the IRQ line, and then headers to get at all the other pins, along with some optional analog tidbits one could use, or not. Like a quad op amp, and some good-but-not-great LED drivers.

davidedelvento, 2022-02-16:
> Hmm, I'd imagined attaching mechanical pots to such things... somehow, and then cables with TRS plugs.

I see. I don't like mechanics, since all the leverage acting the pots need to be within well specifics ranges to operate correctly, but perhaps for just 2 or 3 as in this case it won't be so bad.

In my (*) view of what you are doing, I thought: an ADC measuring a potentiometer isn't that different from an ADC measuring the output of this thing https://www.sparkfun.com/products/11769 (which I am testing as a key sensor). Hence with limited work on your side, this very same board can support either the optical sensors, or the mechanically attached pots, or the commercial pedals based on pots.

(*): probably excessively simplified, as you have certainly noticed by my other comment about the op amp placement

jkominek, 2022-02-17:
> an ADC measuring a potentiometer isn't that different from an ADC measuring the output of this thing

Yeah, that's true. There's no reason I can't stick some headers on this exposing the ADC lines, and bring out the +3V3 rail a couple of times of convenience. I will do exactly that.

> I don't like mechanics, since all the leverage acting the pots need to be within well specifics ranges to operate correctly

That's a good point. Pedals would be moving pots at low RPM, so they'd probably hold up, but there'd need to be some consideration for alignment just to get it working in the first place.

jkominek, 2022-02-17:
Ok, added headers bringing out the ADC lines and some power, in 91a407f.

jkominek, 2022-04-24:
dc4713c marked as rev 2 and ordered

Closed 2022-04-24.

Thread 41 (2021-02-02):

Main Board Rev 2

jkominek, 2021-02-02:
- [x] Generally review the thermal relief on the top layer to ease hand soldering
- [x] Specifically improve the thermal relief around the RS485 transceiver decoupling caps
- [x] Similarly improve thermal relief around the I2C connector decoupling caps
- [x] Fix silkscreen of C20 (decoupling cap for I2C J6)
- [x] We use lots of ferrite beads on this one. The 0805 inductor footprint is a PITA; increase to hand soldering 0805 footprint, or maybe use the non-hand soldering capacitor 0805 footprint.
- [x] BOM for the Pwr and Stat LED current limiting resistors should be adjusted way down. Currently 3300 ohm(!) they should be more like 300 ohm.
- [x] The JTAG header is 33mm x 9mm. It needs a significantly larger courtyard than was used.
- [x] I got the battery connector pinout wrong, because I forgot to look up the connector polarity. Just remove the battery and RTC stuff. There is at least one Qwiic RTC board available from Sparkfun, that should work just fine for anyone who wants standalone operation with correct timestamps on the SD card.
- [x] STM32H7 actually has special hardware support for SD cards. Rearrange UARTS/I2C/etc to get access to one of those sets of pins. Drop the use of SPI6.
- [x] The SDCARD_DET line was hooked up all wrong. Fix that.

jkominek, 2022-02-20:
Changes all made in feeed297. Leaving open for now, while I continue to cogitate.

jkominek, 2022-04-24:
dc4713c marked as rev 2 and ordered

Closed 2022-04-24.

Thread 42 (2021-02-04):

LED power rev 3

jkominek, 2021-02-04:
- [x] Need a bit more thermal relief on the passives connected to the top layer copper pour. They're sort of a pain to hand solder.
- [x] C10 (incoming .1uF on the 48V rail) is just a bit too close to J9
- [x] Why did I use different resistor values for R24 (Vref drain) and R9 (/SHDN pullup)? No reason I couldn't just use some arbitrary value in the 2.2k-5k range for both. Pick something I'm using elsewhere (the dividers?) that actually matters and just use that for both, to reduce BOM.
- [x] R0 is unnecessary for draining the big cap now that we've got the voltage divider on +48V, draining 0.5W all the time (huh, maybe i should up the total resistance of the voltage divider)
- [x] Eliminate the need for the +15V supply, by regulating the +48V down to about +24V with an LM317. Should be cheaper than putting the second screw terminal on the board. The op amps can use the +24V directly, and that should be low enough for the 5V regulator feeding the precision voltage reference. Expected current draw on the whole rail is <1mA, as we're just feeding quiescent currents and the op amps are keeping MOSFET gates stable.
- [x] /IRQ line should be pulled down with a transistor, instead of directly attached to a pin.

jkominek, 2022-02-14:
All of the changes were made in ef2d1cc.

No need to worry about the MCP23017; replaced it with an STM32G0 that has ADC inputs.

Will leave this issue open for the time being, in case I think of anything else I want to change.

jkominek, 2022-02-16:
Switched to a BJT to pull down the interrupt line in 5b2fe51.

jkominek, 2022-04-24:
dc4713c marked as rev 3 and ordered

Closed 2022-04-24.

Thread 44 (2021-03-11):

Sensor board PCB

jkominek, 2021-03-11:
I produced a bunch of variations on the sensor board very quickly, to account for the changes in my mechanical plan. I need to fix up the silk screen and labelling on all of them to make them less confusing. Some more test points would also be appropriate.

Additionally, I'd like to make a variation on some of them that uses the EAITRCA6 from Everlight. It's a similar, but much thinner sensor. Looks like it could be surface mounted, which would allow the sensor PCBs to rest flush against their support. That should eliminate flex when the hammer impacts.

davidedelvento, 2021-03-11:
Another idea on the topic of "avoid hammer impact", especially if the last 1mm is still too close to get any useful data. Have you tried if Plexiglas (or other transparent plastics) are transparent to these wavelengths? Usually these materials tend to be brittle, so they will need some support, but still it can be a viable alternative.

jkominek, 2021-03-13:
> Another idea on the topic of "avoid hammer impact", especially if the last 1mm is still too close to get any useful data. Have you tried if Plexiglas (or other transparent plastics) are transparent to these wavelengths? Usually these materials tend to be brittle, so they will need some support, but still it can be a viable alternative.

I have not, but it's worth giving a go at some point. A thin sheet of polycarbonate glued over top of my 3D printed support would help ensure heavily worn hammers can't slip into the sensor holes. And I'd expect polycarbonate to last forever under these forces.

I'll root around and see what I've got in my piles of materials, and maybe take a quick trip to Home Depot before we're all snowed in. :smile:

davidedelvento, 2021-03-24:
While playing with my hammers alignment, I've got more solid details on the ideas we floated on how to "screen" the sensors from hammer impact.

The first is doable if you can make the 2040-centered-4x for a 30x60 extrusion (which should be pretty easy, since the latter is bigger). This option uses two https://us.misumi-ec.com/vona2/detail/110300466750/?ProductCode=HFSFIL5-3020-500 placed in front of the sensors leaving a slit for the sensor/LED to "see" the hammer. In this design the slit width is adjustable, and hopefully it's possible to make it thin enough to not let the hammers too much in, while at the same time large enough for the sensors/LED to see through.

The other option, would use a 2080 with the sensor board mounted in the two innermost slots of the 80mm side and a number of polycarbonate sheets like https://us.misumi-ec.com/vona2/detail/110302696070/?ProductCode=PCTTA6H-70-70-5-F30-G60-N4 would be mounted on the two outermost slots. Kind of expensive though, so it gotta work well to be worth it.

I can make some sketches if you'd like.

jkominek, 2022-01-09:
It looks like you've already investigated this, but for completeness' sake I'll note that I haven't done anything with other sensors, but I think I do have a few EAITRCA6 laying around. Considering the shape of the leads, I'm not surprised that EasyEDA wouldn't have it, I don't think it could be used in automated assembly.

davidedelvento, 2022-01-09:
I have 10 'CA6 and I doing some tests with it. Already investigated is an overstatement, but I have done something, which I reported https://pianoclack.com/forum/d/243-diy-piano-sensors and in the PR #45

I thought the 'CA6 had another option with regular surface mount seagull leads, but I can't find it at the moment. Alternatively, the QRE1113 could be an option: that comes in two slightly different forms, with either through hole or seagull leads. My results with it haven't been very good, but that was only one sensor and I might have mishandled or broken it, so it's worth investigating for the automated assembly.

jkominek, 2022-02-02:
3d1d8aee updates the 4x versions of the board for the parts of this that I still wanted to do, and introduces a version of the hammer sensor board with the sensors rotated 12 degrees, to make life easier with bass hammers.

And here's a PDF of the footprint for the QRE1113GR. I'm unclear if you had purchased any of them, but if you have, printing this at 100% and checking the correctness would be helpful. It's a non-standard footprint, so I had to make it from scratch, and I like to check parts against a printout before ordering PCBs. (The PCBs are cheap, I just hate wasting the turnaround time.)

[QRE1113GR.pdf](https://github.com/jkominek/piano-conversion/files/7983613/QRE1113GR.pdf)

davidedelvento, 2022-02-02:
I don't have any loose QRE1113GR at the moment, but I do have a couple of them soldered to the SparkFun board (see below). I could print the PDF on transparent paper (I should I have printable transparent plastic slides form the "good ole times", if not I can scavenge for the thinnest, semi-transparent paper I have in home, and hope the printer does not jam). With that, I should be able to check the match even if it's soldered to the board -- if you think it's useful -- since the sensor is thin, it may be better-than-nothing and good-enough.

Otherwise, I am making an order to DigiKey in the next couple of days and I can add one QRE1113GR.

Alternatively, we can do an all-software check with the data at https://github.com/sparkfun/QRE1113_Line_Sensor-Analog which is the board I have.

Yet another option: I have low-quality-but-usable setup to take super-close-up pictures, and I can take several of the QRE1113GR attached to the board, and placing close to it my "piano-caliper" (effectively a thinly marked ruler)

Let me know if any of these would be of any use (feel free to switch to email, if you think it's more efficient for this purpose)

jkominek, 2022-02-08:
I picked up some more QRE1113GR. The footprint matches just fine.

I don't have the energy to keep track of what you're doing mechanically; is it sufficient for the new layouts to match the existing ones, just with this sensor replacing the CNY70?

davidedelvento, 2022-02-08:
> I picked up some more QRE1113GR. The footprint matches just fine.

Awesome, thanks!

> I don't have the energy to keep track of what you're doing mechanically;
> is it sufficient for the new layouts to match the existing ones, just with this sensor replacing the CNY70?

I think mechanically I am doing exactly what you are doing:
- Place the same 40mm extrusions (with tracks at 20mm from each other) in front of the hammers. The hammers are aligned in such a way to hit the centerline between the tracks.
- will use a plastic "hammer stop rail" similar to yours in front of the sensors (obviously with smaller holes)
- for the 4x boards, the average distance between the centers of the hammers is 12.6mm and the section averages may go as high as 13.0mm and as low as 12.2mm (individual outlier pairs go even up to 15mm, but probably I should regulate them or use individual sensorboard for them) -- this variability is what I had in mind [here](https://pianoclack.com/forum/d/107-cybrid-a-diy-midi-controller-with-grand-piano-action/90)

I was not planning to use the 12 degrees boards, because I see my hammers do not all have the same orientation (which I have not measured). Heck some are even oriented in the opposite direction! If it cost you zero effort, make those too which might turn useful anyway to me or to someone else, but otherwise only the "straight" boards will suffice.

Thanks a lot!

davidedelvento, 2022-06-23:
Have you placed the QRE1113GR (or EAITRCA6) footprints in kicad_mod format anywhere in the repo?
I'm trying to make PCB of the sensorboards with either of them and I can't find the appropriate footprint, but you must have made it already, since you posted the PDF in this thread.
Thanks!

jkominek, 2022-06-23:
Here's the one I made:

[QRE1113GR.zip](https://github.com/jkominek/piano-conversion/files/8967487/QRE1113GR.zip)

But I believe it is identical to the builtin footprint for the "OnSemi_CASE100CY", in the OptoDevice library. (Thought I mentioned that somewhere, but I can't find a record of it.)

davidedelvento, 2022-06-23:
Great thanks! Now I need to figure out the headers and mounting holes, which KiCad apparently cannot find (sigh)

```
Error: Cannot add J1 (footprint 'Pin_Headers:Pin_Header_Angled_1x10_Pitch2.54mm' not found).
Error: Cannot add H6 (footprint 'Mounting_Holes:MountingHole_3.2mm_M3' not found).
Error: Cannot add H5 (footprint 'Mounting_Holes:MountingHole_3.2mm_M3' not found).
Error: Cannot add H4 (footprint 'Mounting_Holes:MountingHole_3.2mm_M3' not found).
Error: Cannot add H3 (footprint 'Mounting_Holes:MountingHole_3.2mm_M3' not found).
Error: Cannot add H2 (footprint 'Mounting_Holes:MountingHole_3.2mm_M3' not found).
Error: Cannot add H1 (footprint 'Mounting_Holes:MountingHole_3.2mm_M3' not found).
```

davidedelvento, 2022-06-24:
If others have the same problems, I found the holes at https://gitlab.com/kicad/libraries/kicad-footprints/-/tree/master/MountingHole.pretty and the headers at https://raw.githubusercontent.com/KiCad/Pin_Headers.pretty/master/Pin_Header_Angled_1x10_Pitch2.54mm.kicad_mod -- note that the latter are from an older version of KiCad, because newer versions don't have that. Current v6 loads it ok, See https://raw.githubusercontent.com/KiCad/Pin_Headers.pretty/master/README.md for details. It seems to work, but I am not sure if there are some unintended consequences.

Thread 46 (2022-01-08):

Scanning frequency analysis, per channel.

davidedelvento, 2022-01-08:
According to this paper http://mtg.upf.edu/mosart/papers/p35.pdf and this other one https://www.researchgate.net/publication/7603558_Touch_and_temporal_behavior_of_grand_piano_actions and how it discussed in some details at
https://pianoclack.com/forum/d/289-scanning-speed-and-velocity-mapping-of-cybrid (and to less extent https://pianoclack.com/forum/d/243-diy-piano-sensors/33 ) it might be necessary to scan at 200kHz per channel.

jkominek, 2022-01-09:
Hmm. I had not thought about the timing in the context of the letoff. (And have not yet reviewed the provided materials enough to convince myself of the accuracy, but at glance it is concerning.)

As it stands the ADCs scan all the channels at the same rate. The firmware could, possibly, dynamically change the sampling rate. It could shift to sampling only one channel at a time when they're in the terminal stages of a >=forte hammer strike.

(There are other options, but that would be the "cheap" one.)

davidedelvento, 2022-01-09:
Yes, I have not convinced myself of what is really needed yet, but I wanted to put the discussion out there for you and others to see before anybody invests too much (time or money) in something which might be a dead (or subpar) end.

jkominek, 2022-01-09:
From a hardware design/posterity standpoint, my initial thought is:

1. Assume we only need this very high speed sending for hammers, not for key sticks/damper motion.
2. Lift the whole analog stage onto a daughterboard, intended to mount tightly to the ADC board.
3. Keep the TIA-configured opamps we've got, but then also add analog differentiators for 11 of the inputs. Those would be the hammer inputs.
4. Add two 16:1 analog switches/multiplexors. Each one would be connected to all of the differentiator outputs. So we'd be able to listen to any 2 of the hammer signals we wanted, differentiated.
5. The STM32H743 has two ADC inputs which are super high speed. Connect the analog switch outputs to those. Take all of the other analog inputs off of the corresponding ADC converter, and consolidate them on the remaining two other ADC converters. The sampling rate for those converters would drop further, but we'd just be using them to determine roughly when we're about to hit a "string" with a hammer, at which point we'd command the analog switch to feed us the differentiator output for that hammer. I'd have to recheck all the specs, but those high speed inputs should be able to get a high resolution measurement of the differentiator output, very quickly.

jkominek, 2022-01-12:
Pretty sure I can't actually squeeze on two more channels. So the above plan would have to be a single analog switch. And I think the firmware for flipping one of the high speed ADCs into that mode would be gnarly, at best.

Any thoughts on how fast the key stick/damper measurement needs to be? Seems to me that for measuring damper movement, we might be fine in the 100Hz range, but spatial resolution would be more valuable?

If I could drop 11 ADC channels off the STM32 onto some inexpensive external ADC. That would easily leave enough room on the STM32 ADCs and their input channels to accomplish the above. The high speed inputs could just stay in that mode, and probably hit >1MHz sampling, while the 11 always-on hammer sensing signals should be able to at least double their sample rates.

Reducing the number of ADC channels necessary on the main microcontroller dramatically eases the constraints on that part, as well. If it doesn't need >=22 ADC channels, there are other parts which are physically smaller, cheaper, and faster.

davidedelvento, 2022-01-13:
> Pretty sure I can't actually squeeze

I am not sure I understand the problem, so let me ask some questions. The speed limitation of many of the ST32 ADC channels, if my understanding is correct, come simply because of the extra resistance from the internal multiplexer, which calls for a longer settling time of the voltage. I thought that in your previous comment you were suggesting (among other things) to use a higher quality multiplexer to avoid that extra resistance and hence gain back that speed. Granted, the ADC has a maximum operating frequency, so multiplexing will (at best) divide that frequency by the number of channels, and that might be enough to rule this option out even with a hypothetical zero resistance multiplexer. But I am not sure that is what you are saying.

> Any thoughts on how fast the key stick/damper measurement needs to be?

I am not sure how it *needs* to be, but key sticks move at about 5x slower speed compared to hammers, so I'd argue at least 5x slower sample rate will be ok. However they move about 1/5 of the distance, hence as you say we might need higher spatial resolution. On the other hand, many digital pianos totally ignore this issue, just use one bit spatial resolution (on/off) and according to those documents posted on pianoclack at 90us time resolution. Few people complain about that (I am one of the few), so I guess we can be "sloppy" there and it still should be ok. Hence:

> If I could drop 11 ADC channels off the STM32 onto some inexpensive external ADC.

Tentatively, I'd say that it'll be just fine. We obviously need to run some tests before purchasing hundreds :-) of boards, but I don't anticipate problems.

> Reducing the number of ADC channels necessary on the main microcontroller dramatically eases the constraints on that part

I am not sure I follow you completely, so let me speculate. Are you suggesting a slow sampling for each note and each damper (and option for pedals), so 180 slow channels on an extra board? When those slow suckers detect enough of a movement the relevant input is routed to one of a small number (*) of very fast ADC? From a mechanical/pianist perspective, I think this will work fine, but I am not sure from an electronics pov: you'd need a 180-to-10 mux? You can't simply do 10 mux 18-to-1, because many if not all of the notes in flight could all be in a single one group of 18... Sure we can be smart with the geometry and multiplex notes that are impossible to be played at the same time, but it still looks very complicated to me. My understanding of multiplexing is limited though, so I might be totally wrong here.

(*) Pianists have 10 fingers, and often do not use all of them at the same time, so 10 channels will suffice, or perhaps 20 if we anticipate duets (or very acrobatic playing)

davidedelvento, 2022-01-13:
> The STM32H743 has two ADC inputs which are super high speed.

There are some higher end STM32 which have 3 ADCs (for a total of 36 channels). I almost bought the corresponding nucleo board a few weeks ago, before it went out of stock and so I settled for three RPi pico instead.

jkominek, 2022-01-13:
> I am not sure I understand the problem, so let me ask some questions. The speed limitation of many of the STM32 ADC channels...

Ah. Right, so there are a number of things tied up in there.

For starters, let me note that a very common issue with microcontrollers is that they've got more peripherals, and functionality, than can possibly be used simultaneously with the number of pins they've got. In part because the same die is used in many different packages; the STM32H743 that comes in a 208 pin package can use more of its peripherals simultaneously than can the 100 pin part. The 144 pin part I chose is, of course, in the middle.

The '743 has 3 AD converters, which have between them 36 input channels. I'm pretty sure that on the 144 pin part, a number of those channels come out on the same pin, reducing the practical count. Then some of them might come out on the pins of other things I need, as an example, the debugging pins. (That's an example, I'm not sure that's the case with this design.)

Next, the three ADCs. If you want the ADC to nicely capture samples for you at a fixed rate, and send them to you via DMA (very very important for performance), then all of the channels on that converter have to be captured at the same rate. So if I want to use the two very fast channels at a high sample rate, different from the slow sample rate, then they've got to be the only channels enabled for that converter. That leaves just two converters to do all of the slow sampling, for 22 channels, still.

Given the aforementioned pin limitations, I don't think I can get 11 channels onto each of the two remaining ADCs. Let's see, I'll pull up CubeMX and try to find an assignment...

Nope, can't get 11 channels on each of ADC1 and ADC2. I don't think I could even get 10 on both of them.

> There are some higher end STM32 which have 3 ADCs (for a total of 36 channels).

Yeah, the '743 is one of them. There might be Nucleos using a version of it with more pins, so they'd be more capable. I don't think ST makes any parts with more than 144 in the TQFP package. I don't really care to design with BGA. If you're going to have professional assembly done, they can do it, but it costs more and your yield will go down.

> I am not sure how it needs to be, but key sticks move at about 5x slower speed compared to hammers, so I'd argue at least 5x slower sample rate will be ok. However they move about 1/5 of the distance, hence as you say we might need higher spatial resolution. On the other hand, many digital pianos totally ignore this issue, just use one bit spatial resolution (on/off) and according to those documents posted on pianoclack at 90us time resolution. Few people complain about that (I am one of the few), so I guess we can be "sloppy" there and it still should be ok.

I'm willing to believe that the damper is lifted very quickly, but that doesn't seem very important to me. (I'm open to being convinced otherwise.) It's the return of the damper that seems important, and that's governed by gravity, right?.

I'd like more than 1 bit of damper position resolution, but I can't imagine needing 4 bits of resolution.
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
davidedelvento, 2022-01-13:
> For starters, let me note that a very common issue with microcontrollers is that they've got more peripherals, and functionality, than can possibly be used simultaneously with the number of pins they've got.

Yes, I did notice that and I told to myself: what the heck, they build these things with all of that stuff and then one can't use it all?? Of course I understand the economics of it, and also the size constraints that a smaller package may be more appropriate for some uses.

> Definitely no 180:10 muxes. I don't think such a thing exists commercially.
That's what I thought.

> Moving all of the ADC work onto a bunch of RP2040s is an option along those lines. One could imagine 6 RP2040s on every ADC board, sampling at 250kHz. They'd easily be able to implement the necessary location. Then a cheap many channel ADC for grabbing the slow signals. Or rearrange the whole system, so you have 4 boards with 11 RP2040s each, watching 22 hammers, and then pick up the dampers with some other board(s).

I see. So the RPi pico has not been a bad settling after all :)
So far there's not been shortage of those (yet?) so that's another incidental plus.
FWIW, I think the 9 bits of effective resolution are also adequate. I hope to have a 9-note (very roughly) working prototype in a weekend or two -- MIDI, calibration software et all.

I think the thing that confused me was all this discussion about the slow vs fast ADCs. Sure we can offload the dampers to some other boards with slow ADCs, and perhaps it'd be more economical and/or easier to deal with -- however 4 boards with 11 RP2040 isn't very different from 8 boards with 11 RP2040 and have everything on the same hw and sw. Hence I assumed you wanted to reduce the number of fast ADCs by a on order of magnitude (which makes a big difference) rather than a factor of 2 (which may still be the right thing to do, and we may do it, but it's not a huge difference, at least in my mind).

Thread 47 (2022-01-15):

ADC Board Rev 3

jkominek, 2022-01-15:
Place to record necessary changes for rev 3 of the board:

### Necessary changes

- [x] 4.5V regulator, LP2985AIM5-4.5/NOPB ("SOT-23-5")
- [x] 3.3V regulator, NCP115ASN330T2G ("TSOP-5" which is SOT-23-5)
- [x] 2.0V precision voltage reference, LM4120IM5-2.0/NOPB ("SOT-23-5")
- [x] Rearrange the analog voltage distribution. The phototransistors and op amps should be driven by the 4.5V. The 3.3V for STM32 VAA and op amps V+. 2.0V as Vref+.
- [x] Unify the ground planes, per STM32 EMC doc, and the people who seem to know the most about the subject.
- [x] Double check that we're keeping all of our decoupling cap traces as short as possible.
- [x] Tidy up analog area traces.
- [ ] Do anything else I can learn to do to improve EMC before I feel like having these boards built.
- [x] Adjust USBLC6-2SC6 footprint to also accept MAX3207EAUT.
  * This means shorting some pins together on the PCB. Make the traces for that swing out wide from the part, so they're cuttable when using the USBLC6-2SC6.
  * That'll also mean that you can just leave the part out entirely, which is probably good.

jkominek, 2022-02-06:
Note to myself: We need to keep +3.3VA, as a requirement of the way the STM32 works. I want to bump Vce for the phototransistors up to at least 2V, preferably more. I don't want to run them off the input 5V. So we'll want analog voltage rails of 2V (vref), 3.3V (STM32 and opamps) and 4.5V (phototransistors). That'll leave us with 4.5V-2V=2.5V for Vce.

We'll say the conservative max for +4.5V will be 22 * ~5mA =~ 100mA. 2.0V will draw ~0mA, as it is just maintaining one of the high impedance inputs of an op amp. 3.3V will need to cover the STM32 and op amp circuitry. Maybe call it 50 to 100mA.

I'll abandon the interest in raising Vref; any improvement in "linearity" of the initial sensor signals is worth more.

davidedelvento, 2022-02-16:
> looking for ideas on improving/reducing electrical noise on the ADC board.

How about putting the op amp on the sensorboard? If I am not mistaken you are using parts which have 4 in one chip, so that's a perfect match for the 4x sensorboards.

jkominek, 2022-02-16:
> How about putting the op amp on the sensorboard?

That would require delivering a voltage source to the sensor boards.

I'm pretty sure it would also be worse; the current configuration was a deliberate design choice. The ADC input presents an extremely high impedance, so small amounts of stray charge can affect what it measures. By keeping the opamp output close to it, we make it easier for the op amp to control that voltage.

Whereas on the input side of the opamp, it shows ~0 impedance (because of the TIA configuration), so it would take a lot of stray charge to affect its inputs.

jkominek, 2022-04-24:
dc4713c marked as rev 3 and ordered

Closed 2022-04-24.

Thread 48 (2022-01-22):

MIDI board rev 2

jkominek, 2022-01-22:
- [x] Silkscreen labels for the I2C pin header.
- [x] Reevaluate usage of TLP185(SE, which appears to be globally out of stock.
  * Pretty sure there are some compatible ones. I'll want to double double check the footprint and such, but this item is probably a no-op.
- [x] Convert to using an STM32G0. (And remove the oscillator)
- [x] Replace the open-drain buffer with a transistor. (MOSFET is probably inappropriate considering the switching.)
- [x] Use a transistor to pull down the IRQ lines.

jkominek, 2022-02-16:
Most of these changes have been made in 98d5832. Holding this issue open for a final review and the update to the board rev on the silkscreen.

jkominek, 2022-04-24:
dc4713c marked as rev 2 and ordered

Closed 2022-04-24.

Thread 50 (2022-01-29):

Sensorboards hole spacing

davidedelvento, 2022-01-29:
All the centered sensorboards have the holes at a distance of `20.2mm` from each other, rather than exactly `20.0mm` as I was expecting for the extrusions you and I are utilizing.

This might be intentional or my own measurement error, and in any case not a big deal since smaller than mechanical tolerances, but since I saw it, I am reporting it anyway.

jkominek, 2022-01-29:
Thanks, probably bumped things around at some point when laying them out. I've added this onto the checklist for #44

Closed 2022-01-29.

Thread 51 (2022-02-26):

HDLC code should use DMA for transmit

jkominek, 2022-02-26:
The HDLC code on the ADC board (which will need to be generalized for use on the main board as well), currently receives data over the UART using DMA. Character recognition on the HDLC frame byte is used to trigger a UART interrupt to process the received data. Works great.

But the board still uses the dumb method of sending data, with the CPU spinning while it waits. Even at 3Mbps the UART is very slow compared to the CPU (480MHz vs 300kB/s). We're burning 1600 CPU cycles for every byte, once the FIFO fills up.

Instead, we should maintain a circular buffer for DMA transmit. Note, we don't want to put the DMA transfer into actual circular mode. Rather, the send function should tack bytes onto the end of the buffer, and if no transfer is currently in progress start one. Then the DMA transfer complete interrupt handler should check to see if there are unsent bytes in the buffer, and if so, begin a new transfer.

(The code which writes into the outgoing buffer could also add in a bit of smarts, and send fewer HDLC frame bytes, depending on what it sees in the buffer already.)

That should free up quite a bit of CPU time, and work quite nicely even with the priority of the DMA transfer lowered, as the UART has its own FIFO to help smooth things over.

jkominek, 2022-06-05:
implemented in 62145be

jkominek, 2022-06-05:
nope, sporadically bugged.

jkominek, 2022-06-05:
ok, 821dc32 appears to take care of it, even under some load testing.

Closed 2022-06-05.

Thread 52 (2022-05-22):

Scoring the sensorboards?

davidedelvento, 2022-05-22:
Most PCB manufacturers have a minimum size, which is much larger than even the larger sensorboards.

I guess making one PCB with scoring should solve this issue (and perhaps save some money, the way I've seen costs being calculated).

I don't see scored sensorboards in the repo though, so I am wondering if that's simply left as an exercise to the reader, or if there is any issue which my naive competence does not let me see.

davidedelvento, 2022-07-25:
Closing this issue, many PCB manufacturers prefer doing the scoring "as they want" with no action from the customer

Closed 2022-07-25.

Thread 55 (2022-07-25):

Cables

davidedelvento, 2022-07-25:
Would using these parts make the ADCboard to sensorboard cables easier to build?

Cable: https://www.digikey.com/en/products/detail/3m/HF100-40TP/3911407
Connector on the ADCboard side: https://www.amazon.com/dp/B00K2NTSJE/
Connector on the sensorboard side: regular jumper to be crimped, such as https://www.digikey.com/en/products/detail/harwin-inc/M20-1160046/3919438

This will cut in half the number of pins that need to be crimped (yay... but see below for even better) produce neatly organized cables (yay), and give some screening protection from noise by virtue of being twisted (yay).

I looked (not very hard) for single-row of stuff like https://www.amazon.com/dp/B0936Q6BDX/ which would eliminate the need of crimping.... or we can use two rows connectors rather than single row on the sensorboard too?

Now of course not everything will fit into the 4x arrangement (I'm planning to leave some of those sensors unconnected), so some cable-fu is still needed, but not as much as if we'd be wiring all 176 sensors (each with two cables, each with two ends) with a regular crimped connector. Am I missing something?

Note that if necessary the HF100-40TP cable can be ordered with custom lengths so we could make the distance board-sensor fully twisted and order an custom section of non-twisted part for ease of separating into the various sensorboards.

jkominek, 2022-07-25:
Huh. Something like that could work. It's 22 pairs, though, not 20. I'm under the impression that IDC crimping is sort of fiddly, so I'd assume I was going to have some wastage if I tried it.

> we can use two rows connectors rather than single row on the sensorboard too?

Certainly some sort of cable-fu would be required to make things line up.

There's probably some way to do something. I look forward to seeing what you come up with. 😃

davidedelvento, 2022-07-25:
According to https://blog.samtec.com/post/idc-or-crimp/ IDC are easy and reliable if you buy high quality parts.

They also have the 22 pairs (thanks for pointing it out) and the 8 in single row, so the parts are available.

They would even assemble it for you, and I assume that would be relatively inexpensive. However they default assembly configurator assumes you want the same connector on both ends (but can mount only one if desired). Most notably, they don't have the 3M HF100-40TP cable.

As soon as I complete the PCB for the sensorboards, I'll start playing with this.

davidedelvento, 2022-07-26:
Which of these scenarios do you anticipate?
1. connect each pair of sensors (hammer and key) to the same ADC board, which implies
  * a slightly more complicated firmware is running on each ADC board, but they are all the same and they know everything about one note, so probably easier to debug and less work for the main board, _and, most relevantly for this issue_
  * each ADC board will have cables of different length to reach the differently placed hammer and key sensors _or_
2. connect hammer sensors to one ADC board, and key sensors to another which implies
  * a slightly simpler firmware running on each ADC board, but they are of two kinds (hammer and key) and they need to coordinate somewhat about each one note, so probably harder to debug and more work for the main board, _and, most relevantly for this issue_
  * each ADC board will have cables of one length to reach either the hammer *or* the key sensors

davidedelvento, 2022-08-08:
The use of 1-row connectors on the sensorboards and 2-row connectors on the ADC boards makes the ribbon-like approach probably too complicated (for people who don't know what I am talking about see [this](https://forum.digikey.com/t/ribbon-cable-pitch-vs-connector-pitch/248) article).

In hindsight (and for the people coming here in the future) I'd have made the sensorboards with 2-row connectors like the ADC boards (unfortunately they've just been manufactured, even if I don't have them in my hands yet as of now) -- much, much easier to do even if the number of terminations needed to be different (the ribbons could have been split, or more than one ribbon used per connector, which should be doable).

I'll keep experimenting and updating this issue, in the hope to find a good solution which does not involve tossing the sensorboards I have, nor manually crimping 176x2 pin terminations (this assumes that I do use IDC for the ADC side of the cables, otherwise it'll be 176x4 ugh)

davidedelvento, 2022-09-03:
More details on this later, but meanwhile, pictures

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

davidedelvento, 2022-10-09:
A quick report and a question.

I've made quite a bit of tests and I have not found anything that is "the perfect solution", however I've found a couple that can be adequate enough.

One is simply buying premade DuPont jumper cables of the appropriate length and gender -- one has only to twist them. One could buy them in ribbons and separate them: probably cheaper, but tedious and potentially prone to ruining some during the mindless separation (2 sensors per key, 2 cables per sensors that's almost 400 wires to separate). Alternatively one can buy individual cables. With this option one can use the individual housing for each connector, or the ones that can house more than one connector. A bit more complicated than I like to do the latter, but doable.

The other option involves IDC, however not the pre-twisted ones I looked at initially, which for a variety of reasons I did not find a good match. So this option too would involve a lot of manual separating and twisting. The advantage compared to the premade DuPont option is that one can use the appropriate connectors much more easily, and the appropriate cable length.

Yet another option would be to crimp DuPont jumper cables by hand. I find this too much work and discarded it too.

So in conclusion I would go for IDC or premade DuPont jumper cables, in either case twisting them by hand.
The question I have is about stray resistance. I've found that IDC connectors have a spurious resistance between nearby wires typically into the 40MOhm, and not infrequently as low as 10MOhm. I speculate that among the 400 needed wires one or two might even go as low as 1MOhm. Is this going to be a problem? Looking at https://github.com/jkominek/piano-conversion/wiki/Analog-Stage-Theory-of-Operation that resistance would be between emettitor and collector of phototransistors, either or both the *same* one, or a pair from two adjacent keys. As far as I can understand that circuit, this spurious resistance would just add a constant current which can be easily removed as part of the calibration, but I am not 100% sure hence my question.

davidedelvento, 2022-10-23:
Both crimping and IDC turned out to be too much of pain and time sink for me, so I settled on what I think is the easier and faster and does not require either. It does require a lot of twisting, and I'm investigating if I can reduce that, but otherwise, I'll leave with it.

I bought a bunch of pre-crimped cables at Pololu of all the various, appropriate lengths I needed. Available [here](https://www.pololu.com/category/72/female-female-wires-with-pre-crimped-terminals)

I also bought a bunch of connector [housing](https://www.pololu.com/category/70/crimp-connector-housings) in one and two rows. The former for the sensorboards, the latter for the ADC boards. The number of positions also were strategically chosen so that one final cable assembly connects two sensorboards (hammer and key) to is ADC board on a staggered mode: hammer-key-hammer-key-etc

Twisting the 12" cables which go to the sensorboards at the key is a bit tricky and I am still perfecting the technique, but I'm improving. One key to the success of the "perfect twist" is to not only twist the pair around each other, but to twist each cable on its own axis. When done properly, it results in a fast, stress-free, easy-to-bend pair, such as the orange gray on the picture below. If not done at all, it will result in a holy mess which will want to spring back in its untwisted position. When done so-so it will result in something that wants to make loops, has some internal stress, and is somewhat difficult to put in the position one may want, like the red-black and blue-yellow long pairs in the picture below. Note that the short pairs are much easier and forgiving to twist.

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

Probably it's clear and does not require a picture, but here is the detail of the 2-row ADC connector and its nearby connector for the sensorboard going to the hammer

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

And here is how I plan to assemble them, for now with a paper mock of the actual ADC boards:

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

Building a cable serving 4 notes, like the one shown in the above pictures, is comprised of 16 wires: 2 sensorboards (hammers and keys) each with 4 sensors; each sensor has two wires. It took me slightly more than 30 minutes, 15 of which twisting the 12-inch wires, and 10 minutes twisting the short cables (in the picture shown is 2 inches, but in other situation I will need 1 or 3 inches). It took me total 10 minutes to put the connectors inside their own housing: when the cable is twisted it's trickier than I thought.

If I don't improve my skills, that will take me 11 hours of work, which is reasonable but on the "I wish this was faster" side. I suspect I could reduce the time by 30-50% by improving my skills, but again that's still about 6h of twisting, which is too much. I am thinking of a LEGO-Technic basic jig to allow me to twist the cables of the right amount (on each own axis and around one another in the pair as I mentioned above). I will report here if I get any success at that.

davidedelvento, 2022-10-23:
https://www.youtube.com/watch?v=noDwhUSeec4

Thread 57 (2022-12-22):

ADC power supplies: linear or switching?

davidedelvento, 2022-12-22:
An inconsistency in the ADC kicad file:

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

As you can see the comment says "Monolithic switching regulator" but the part and its description is for a linear regulator.

Probably related (hence I am not opening a separate issue for that) is the text in https://github.com/jkominek/piano-conversion/wiki/Assembly-Notes which says

> IF your firmware doesn't draw much current, you can use a linear 3.3V regulator, and save a couple of dollars per board. If you don't know what you're going to run on the board, stick with the suggested VR05S3V3

Not sure what you mean by "suggested", I initially thought that your board had a switching regulator VR05S3V3 which one could substitute with linear regulator, but instead it looks like it is now the other way round? If that is the case, does it mean that the regulator you selected should be able to provide enough current for a generic firmware, or that you measured the current for the firmware you posted and *for that* the linear regulator is adequate?

In any case, you might want to fix the kicad file and the wiki page

jkominek, 2022-12-22:
I'm not entirely settled. Facts:

- I've built them with multiple different switching regulators, including the VR05S3V3 and they all seem to behave fine. (The concern is that they would generate noise that might make it into the analog domain.)
- For the current firmware, TO-220 linear regulators will work alright and the heat generated won't be a problem, even without a heatsink on them. (Linears would make little-to-no noise, but generate waste heat proportional to the current drawn. They're also slightly cheaper.)
- If you got the STM32H7 to sink the maximum rated current, then TO-220 linear regulators even with significant heatsinks would be challenged to remain "cool enough".

So, yeah, the docs aren't completely clear. I'll try to clear that up at some point.

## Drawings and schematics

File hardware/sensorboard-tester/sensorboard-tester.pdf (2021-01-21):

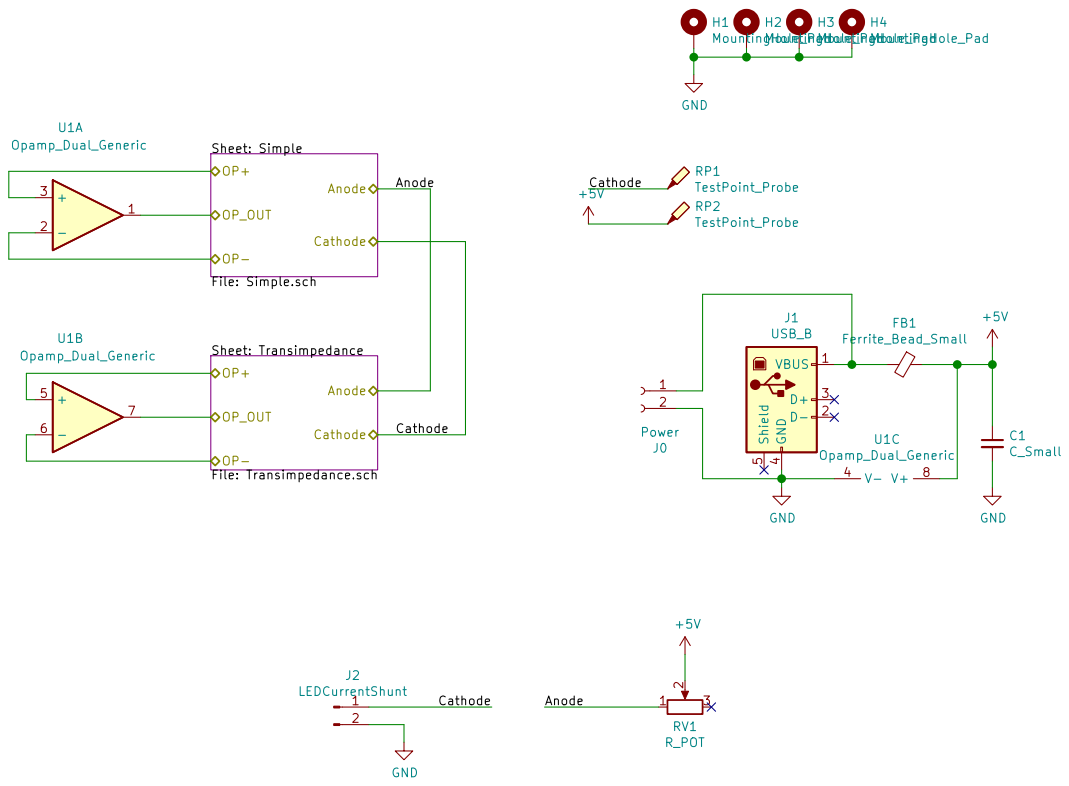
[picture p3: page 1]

Id: 1/3 Title: File: sensorboard-tester.sch Sheet: /

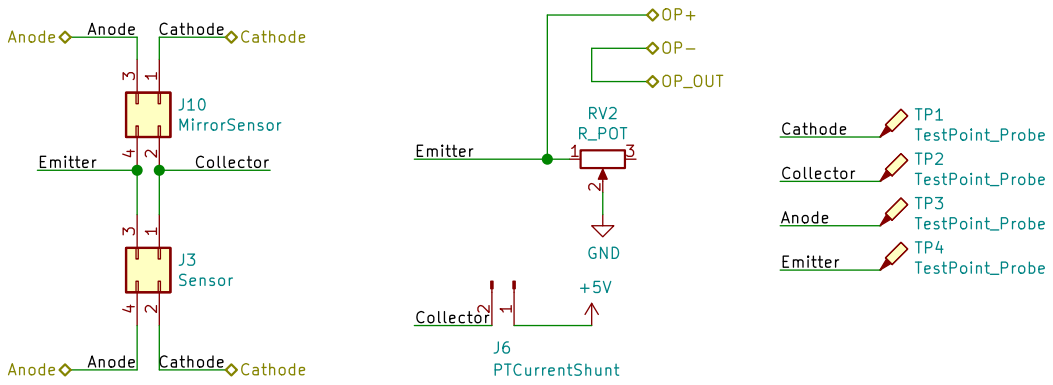
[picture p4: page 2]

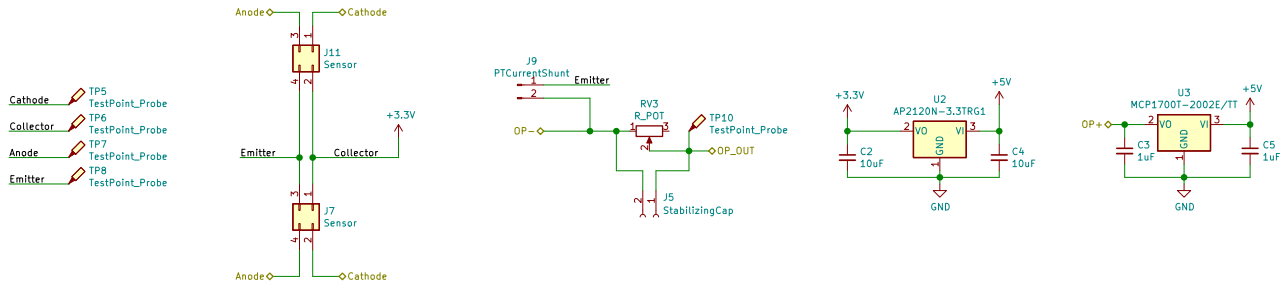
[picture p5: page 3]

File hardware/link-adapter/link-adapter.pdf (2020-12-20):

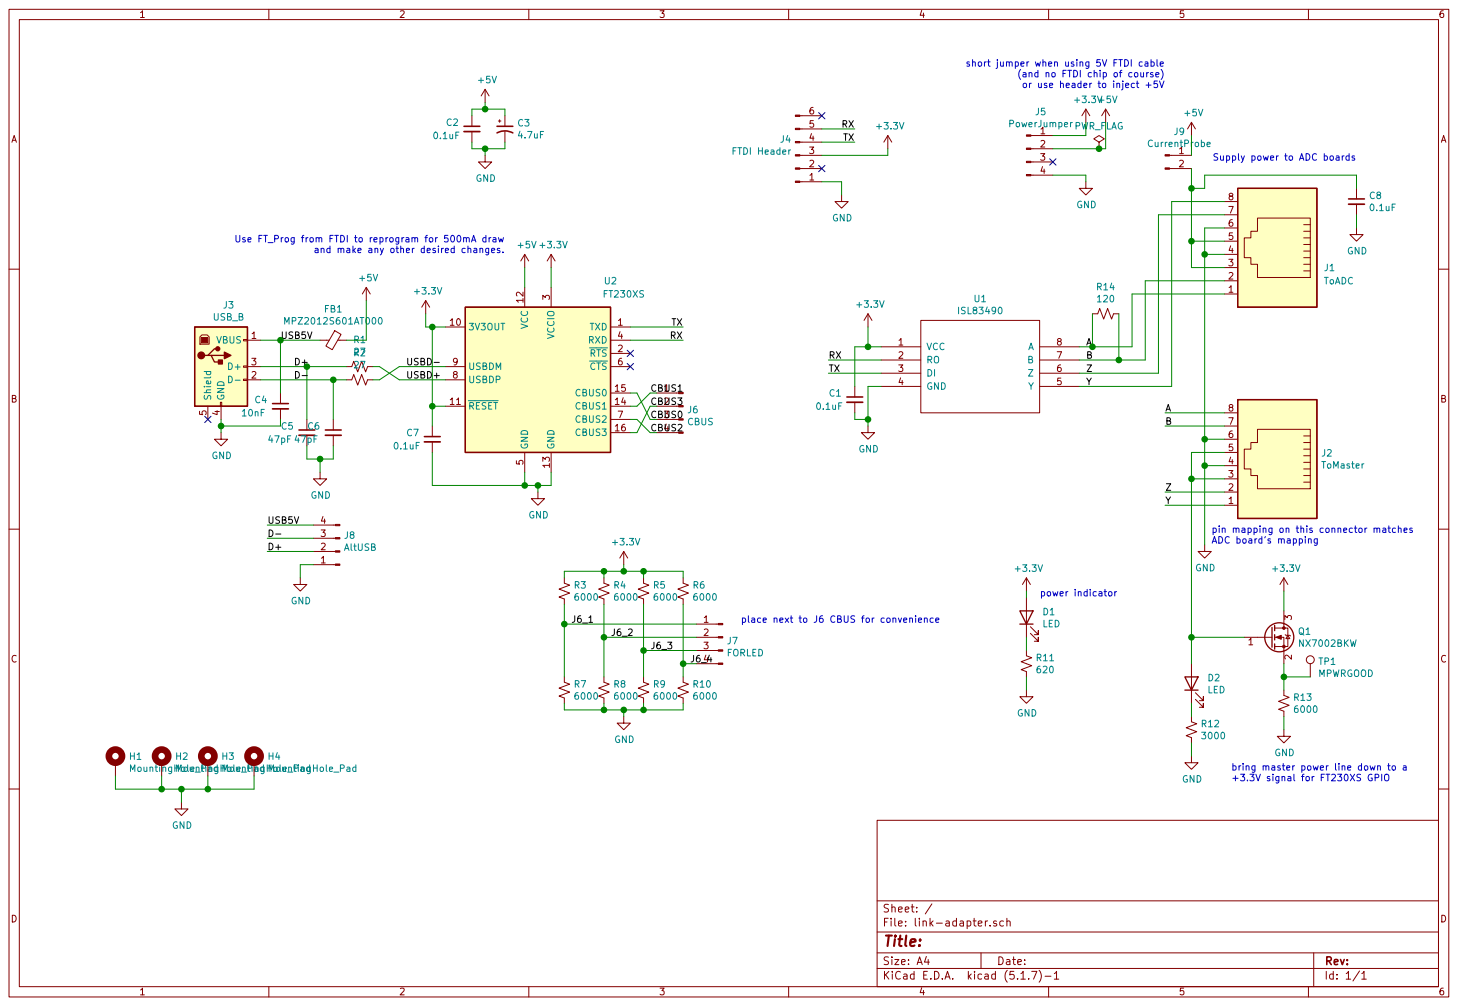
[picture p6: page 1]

short jumper when using 5V FTDI cable

(and no FTDI chip of course)
or use header to inject +5V

Supply power to ADC boards

Use FT_Prog from FTDI to reprogram for 500mA draw

and make any other desired changes.
J1ToADC GND

pin mapping on this connector matches
ADC board's mapping

place next to J6 CBUS for convenience

bring master power line down to a
+3.3V signal for FT230XS GPIO

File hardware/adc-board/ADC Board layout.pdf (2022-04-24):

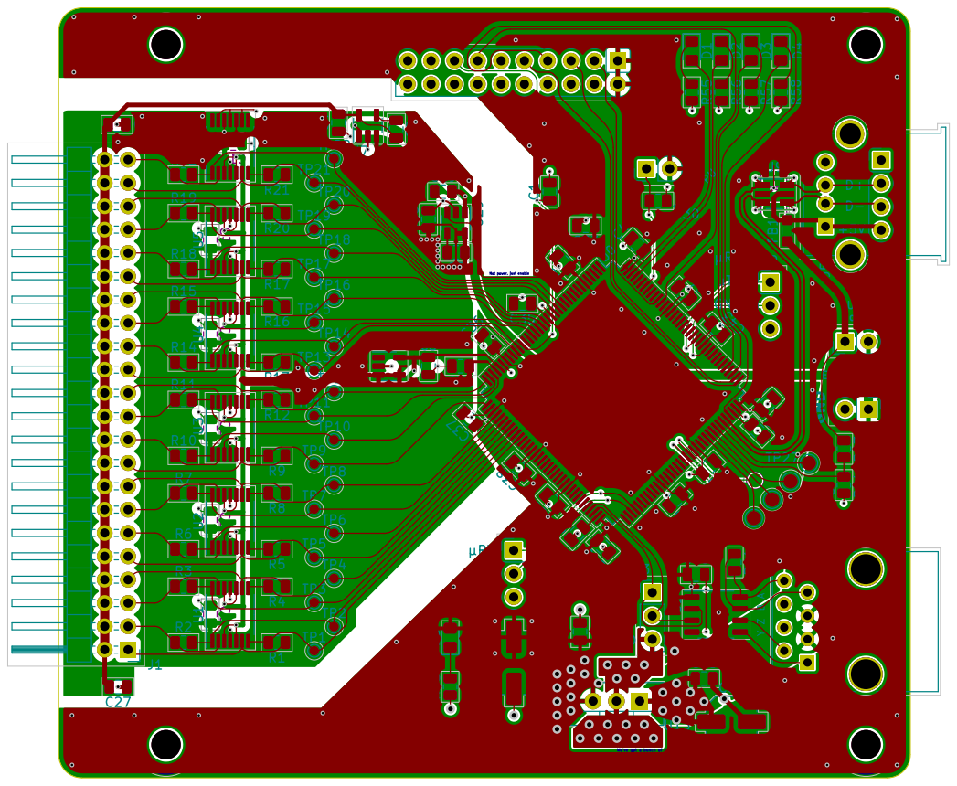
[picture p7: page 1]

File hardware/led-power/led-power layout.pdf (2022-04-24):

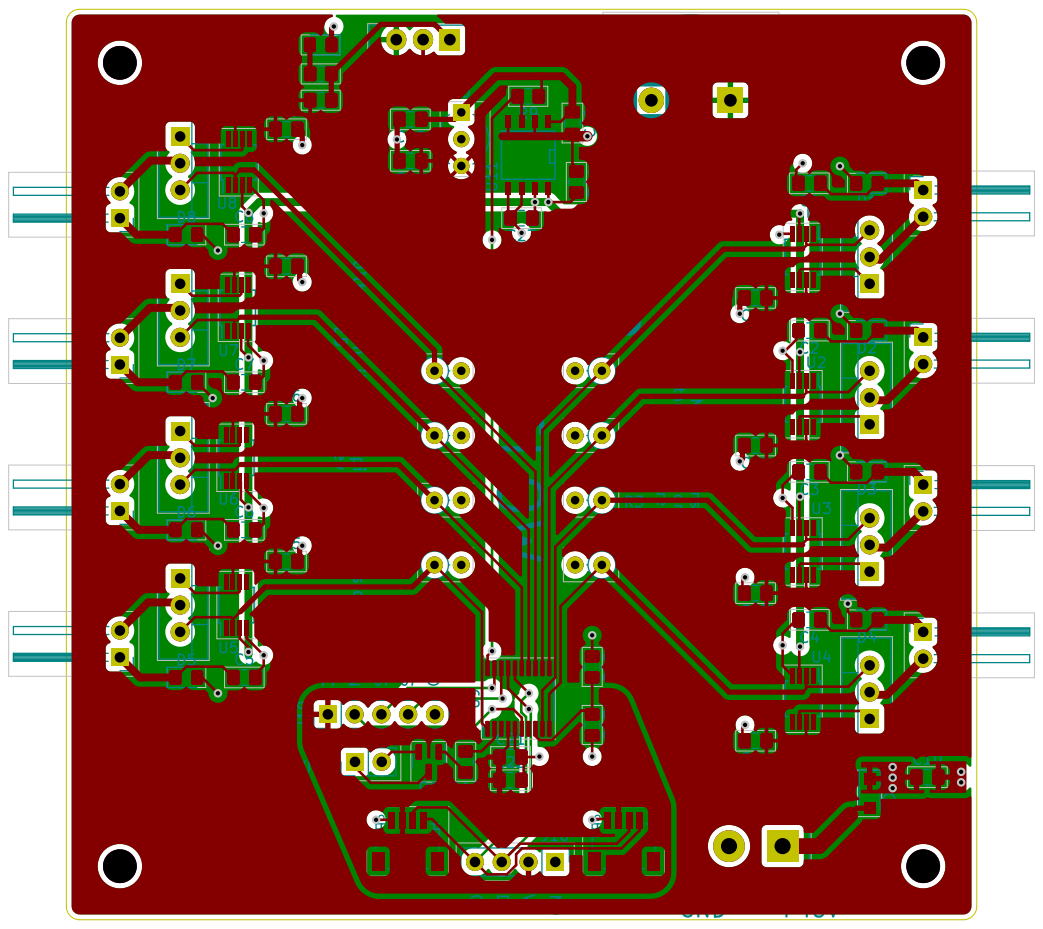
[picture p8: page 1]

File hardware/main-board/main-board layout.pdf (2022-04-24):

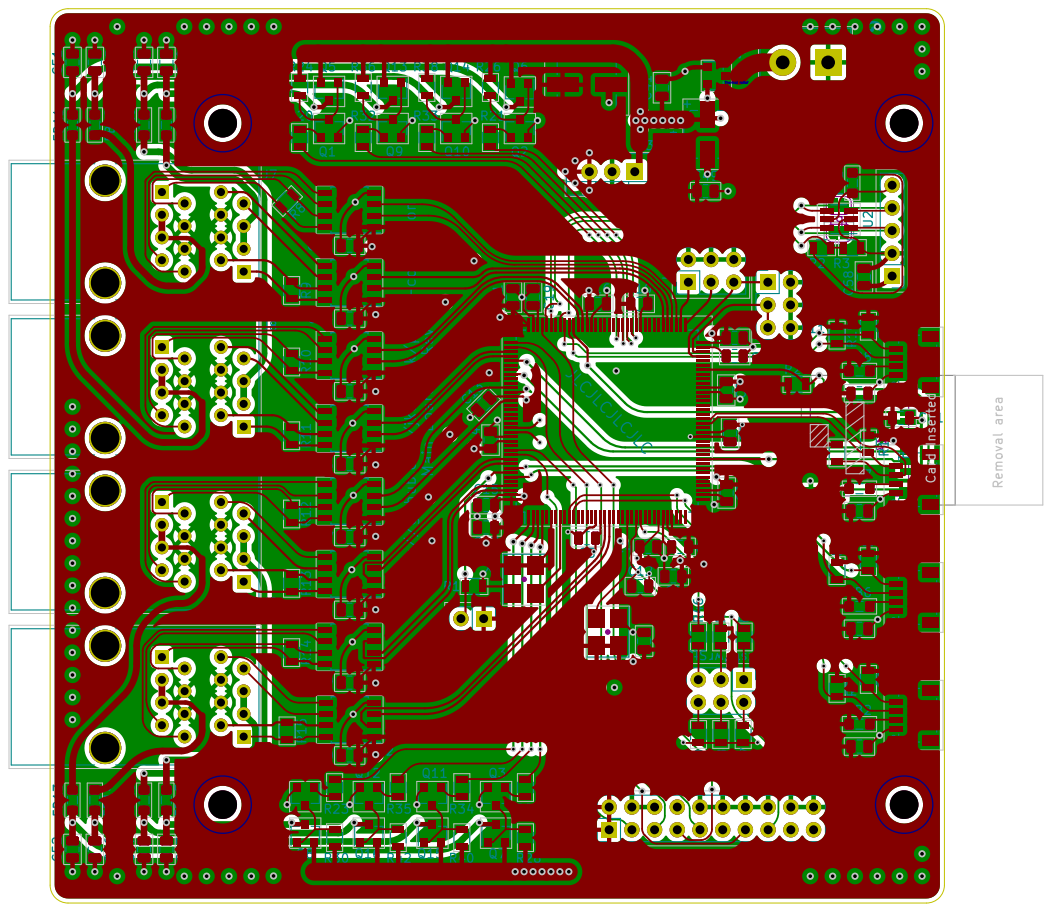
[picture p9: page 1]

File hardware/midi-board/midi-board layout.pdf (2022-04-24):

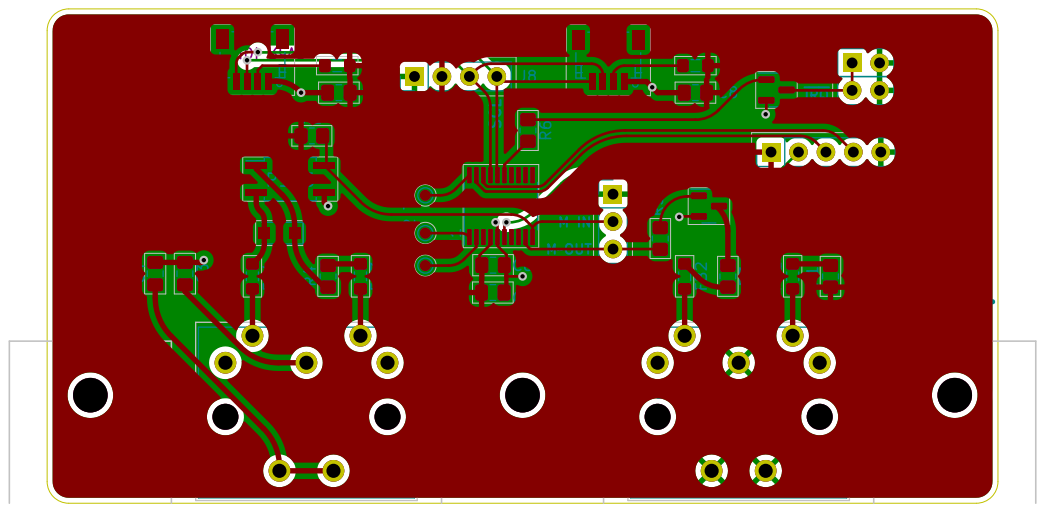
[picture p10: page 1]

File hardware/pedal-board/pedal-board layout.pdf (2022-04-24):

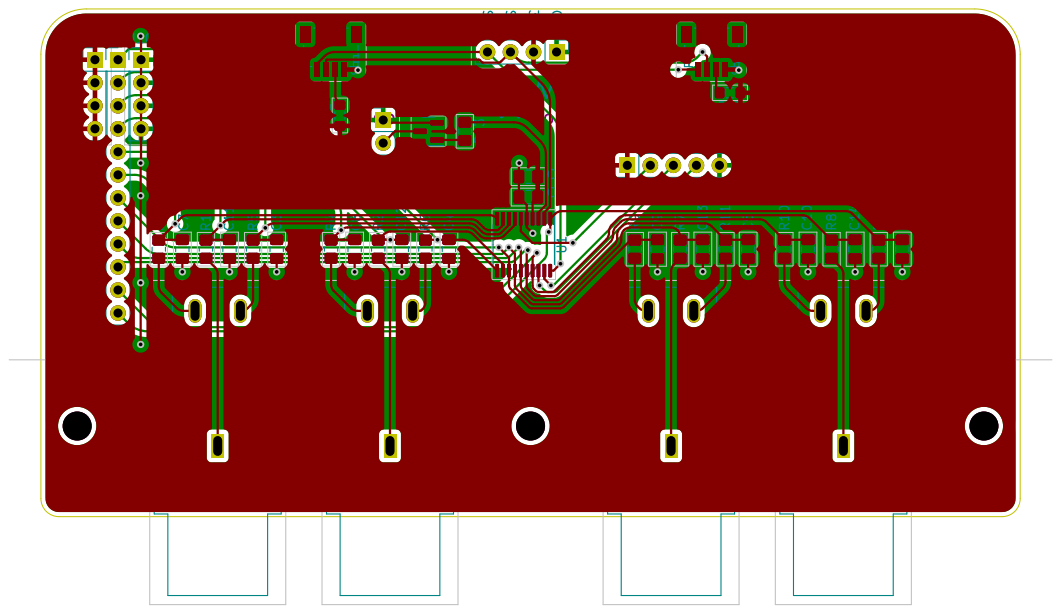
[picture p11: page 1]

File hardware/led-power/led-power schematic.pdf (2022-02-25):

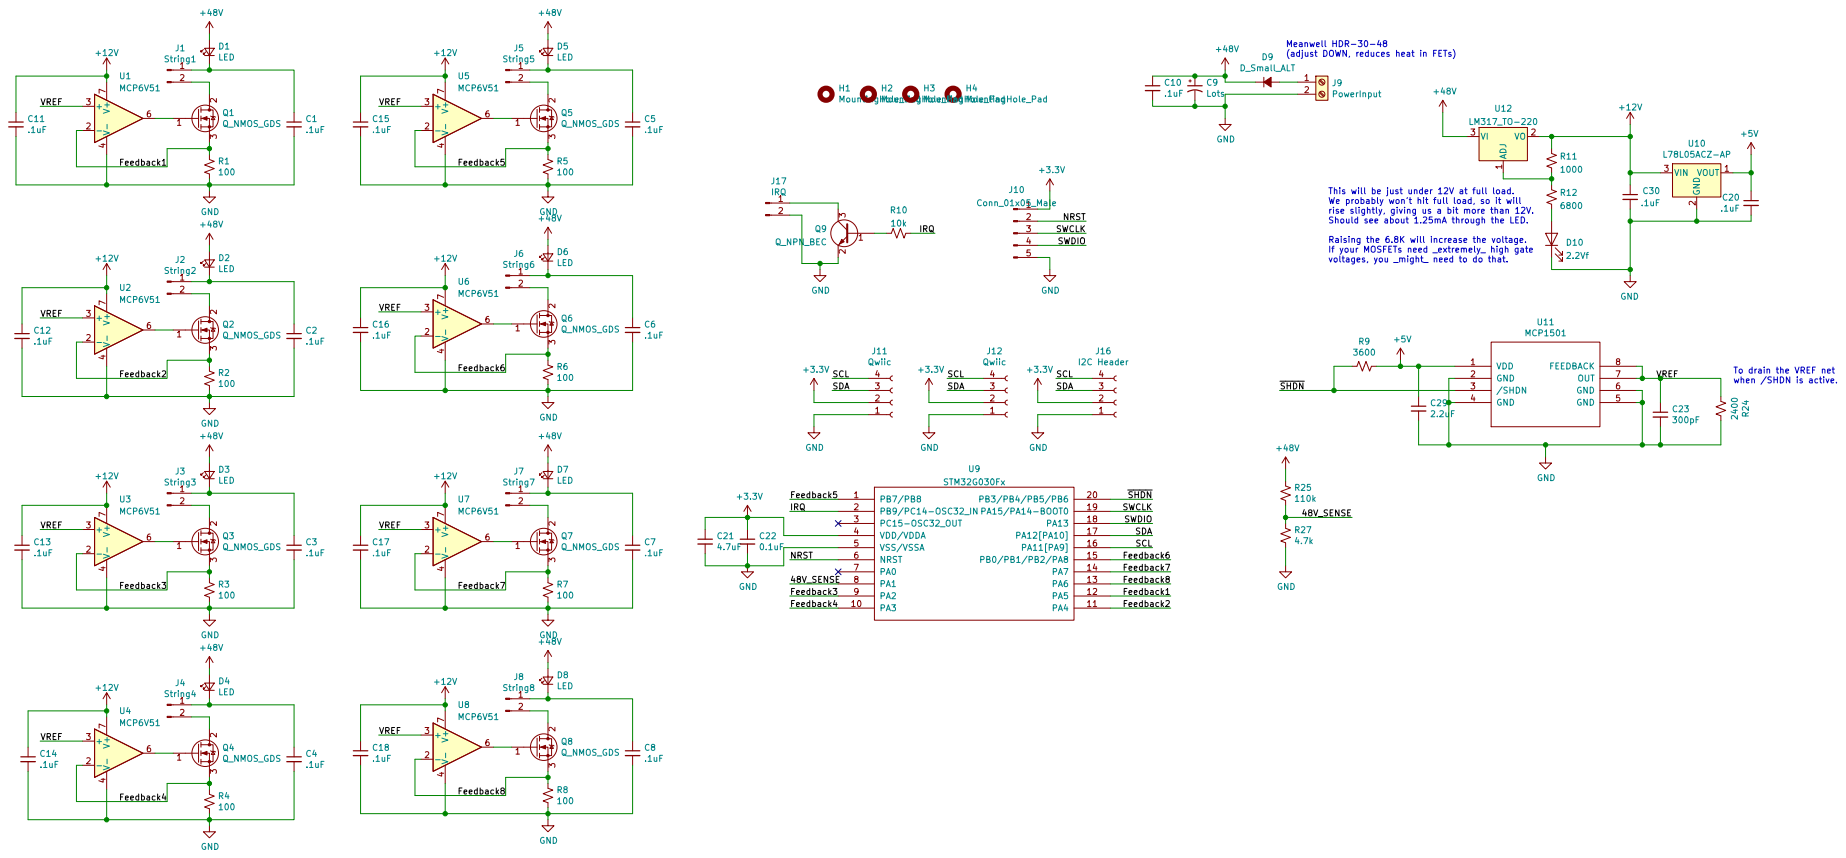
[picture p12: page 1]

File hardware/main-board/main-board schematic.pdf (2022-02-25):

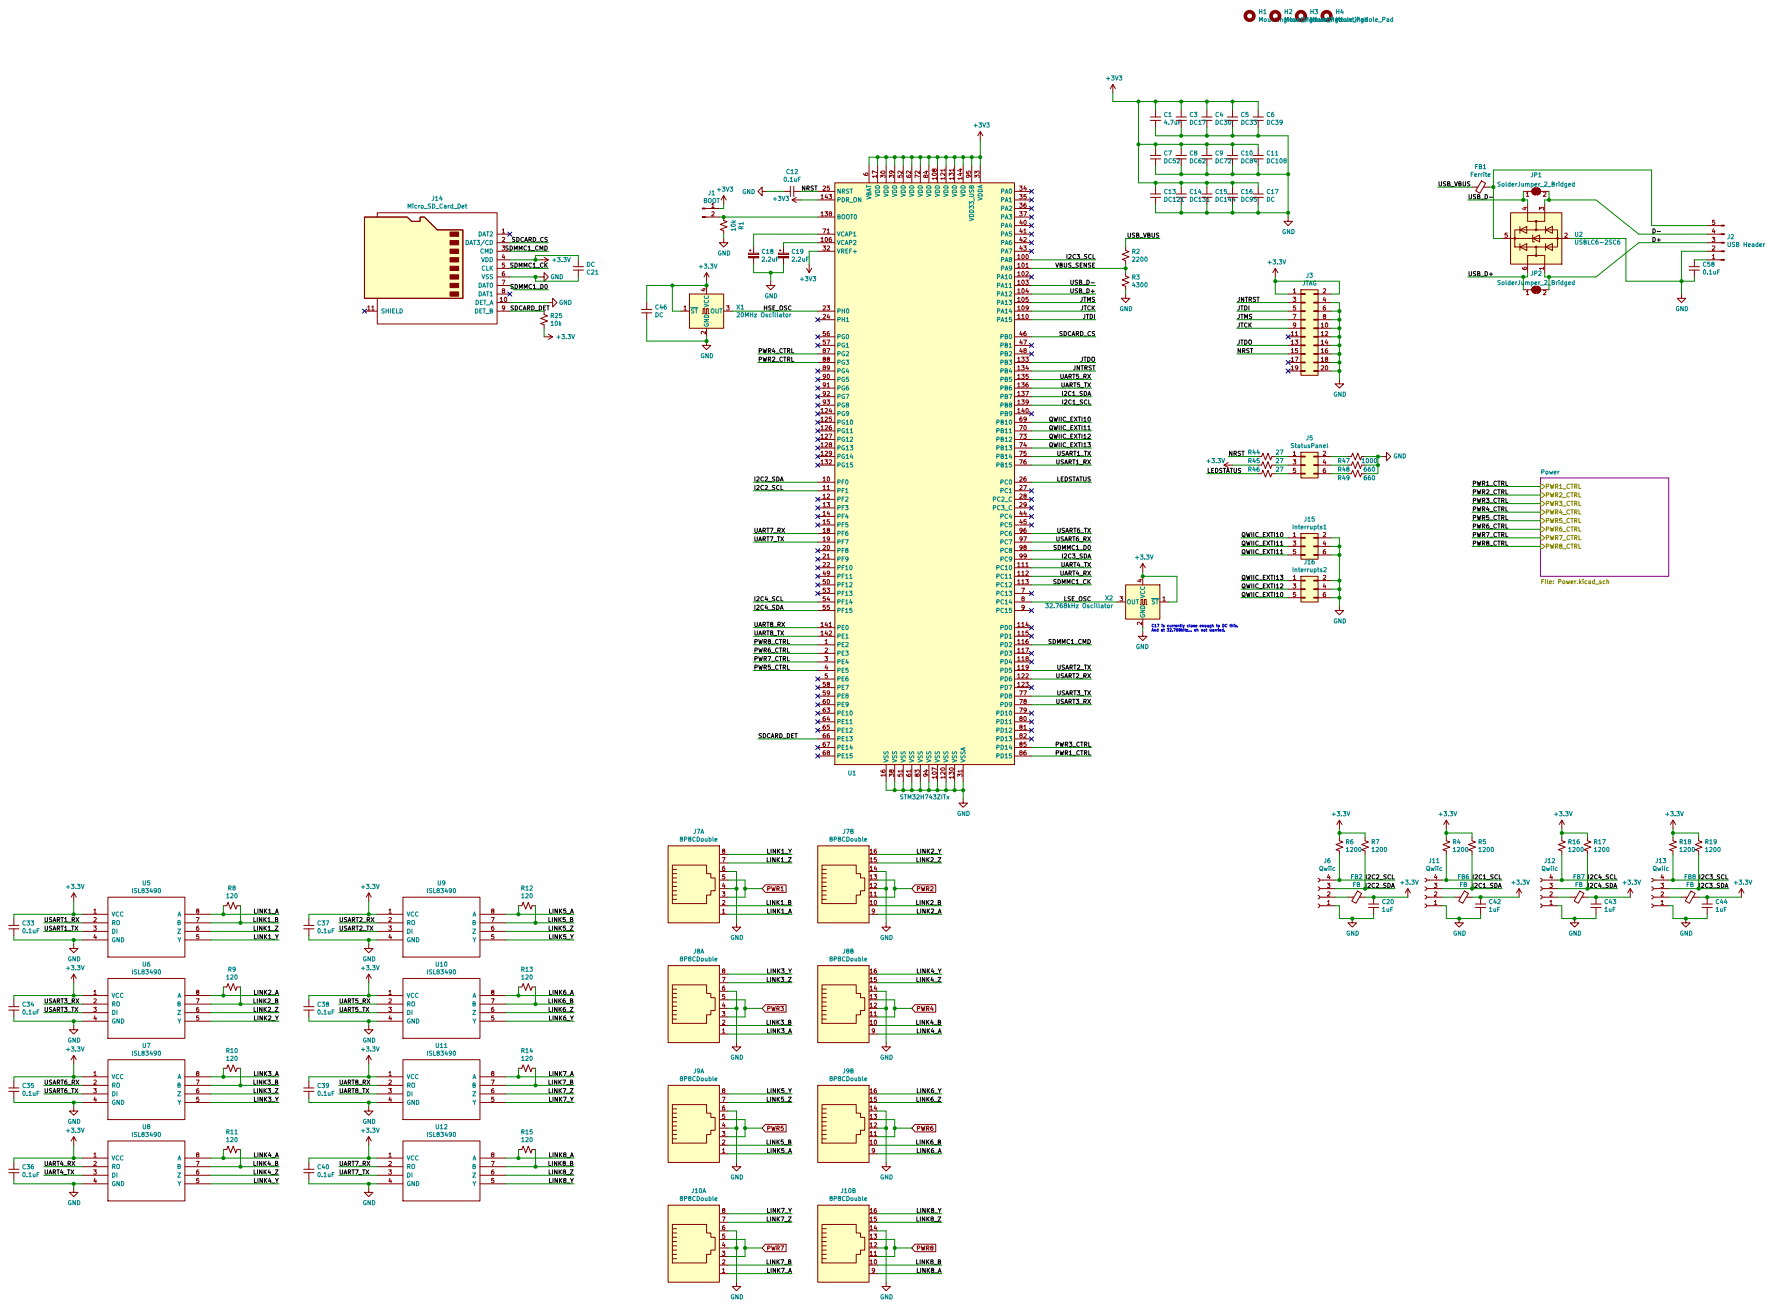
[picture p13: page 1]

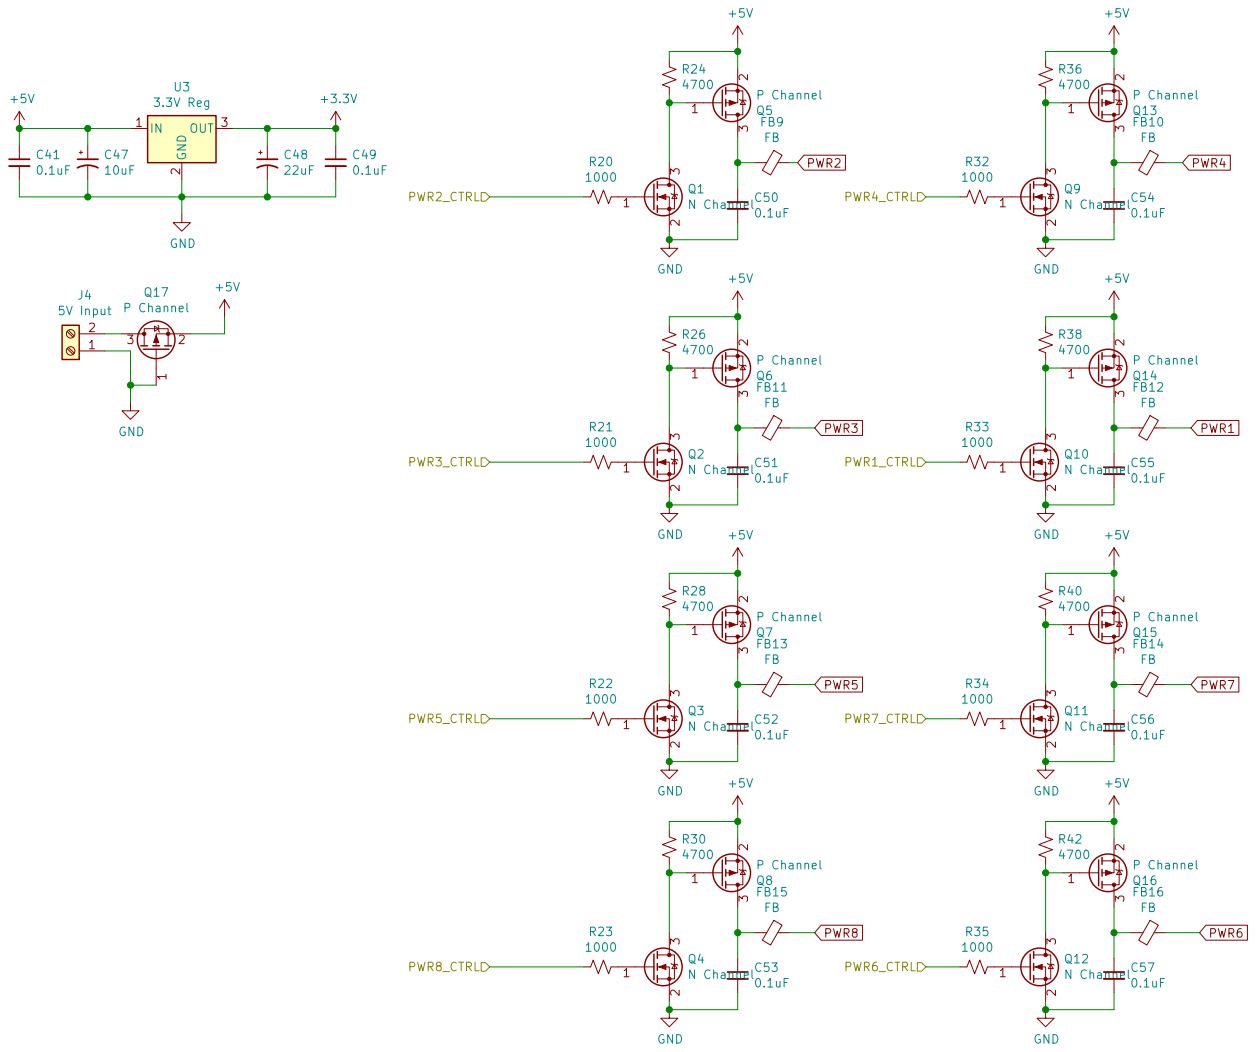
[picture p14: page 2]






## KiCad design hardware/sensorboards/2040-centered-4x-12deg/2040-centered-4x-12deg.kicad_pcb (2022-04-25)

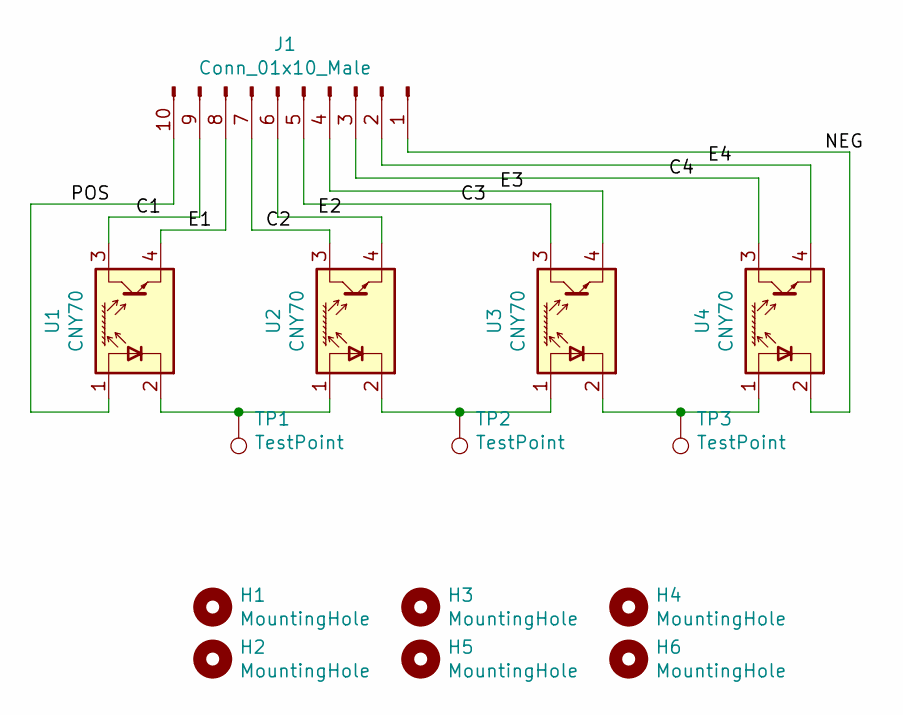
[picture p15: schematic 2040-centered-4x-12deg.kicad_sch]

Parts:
H1, H2, H3, H4, H5, H6: MountingHole; MountingHole_3.2mm_M3
J1: Conn_01x10_Male; Pin_Header_Angled_1x10_Pitch2.54mm
TP1, TP2, TP3: TestPoint; TestPoint_Pad_1.0x1.0mm
U1, U2, U3, U4: CNY70; Vishay_CNY70

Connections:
/C1: J1.9, U1.3 (C)
/C2: J1.7, U2.3 (C)
/C3: J1.5, U3.3 (C)
/C4: J1.3, U4.3 (C)
/E1: J1.8, U1.4 (E)
/E2: J1.6, U2.4 (E)
/E3: J1.4, U3.4 (E)
/E4: J1.2, U4.4 (E)
/NEG: J1.1, U4.2 (K)
/POS: J1.10, U1.1 (A)
unnamed: TP1.1, U1.2 (K), U2.1 (A)
unnamed: TP2.1, U2.2 (K), U3.1 (A)
unnamed: TP3.1, U3.2 (K), U4.1 (A)

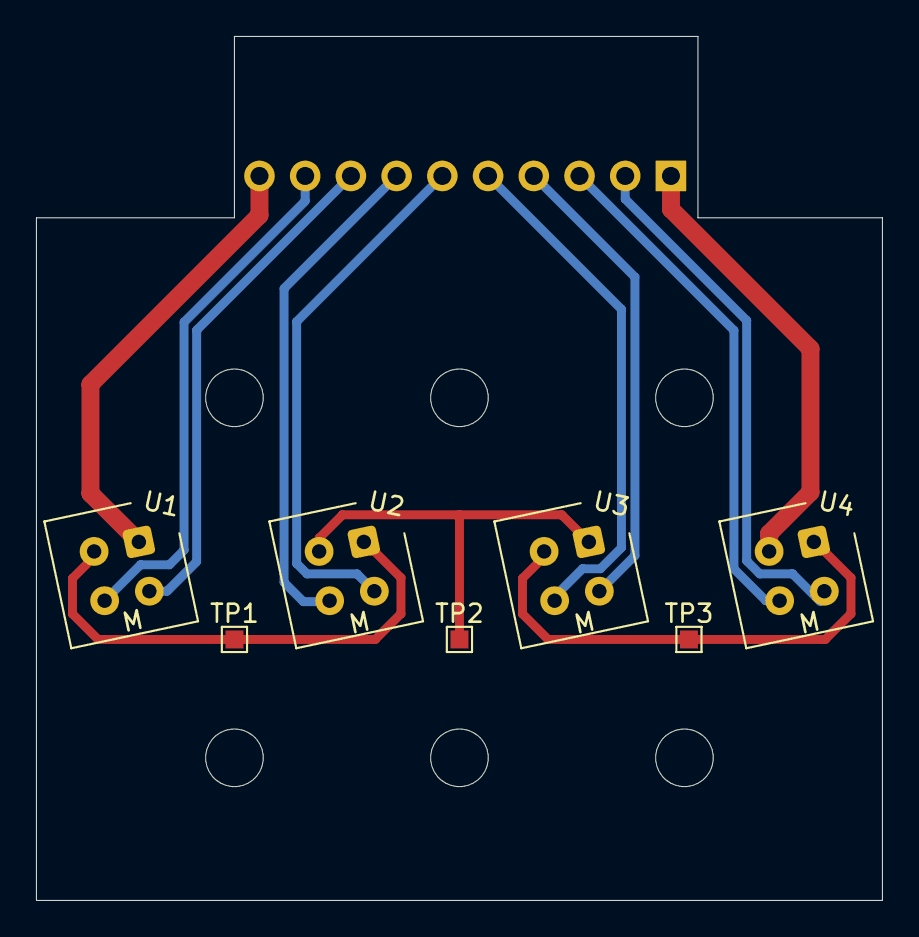
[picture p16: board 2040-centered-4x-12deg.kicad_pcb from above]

Board: 2 copper layers, 47.0 x 48.0 mm, 14 parts (1 on the bottom side), 13 nets.

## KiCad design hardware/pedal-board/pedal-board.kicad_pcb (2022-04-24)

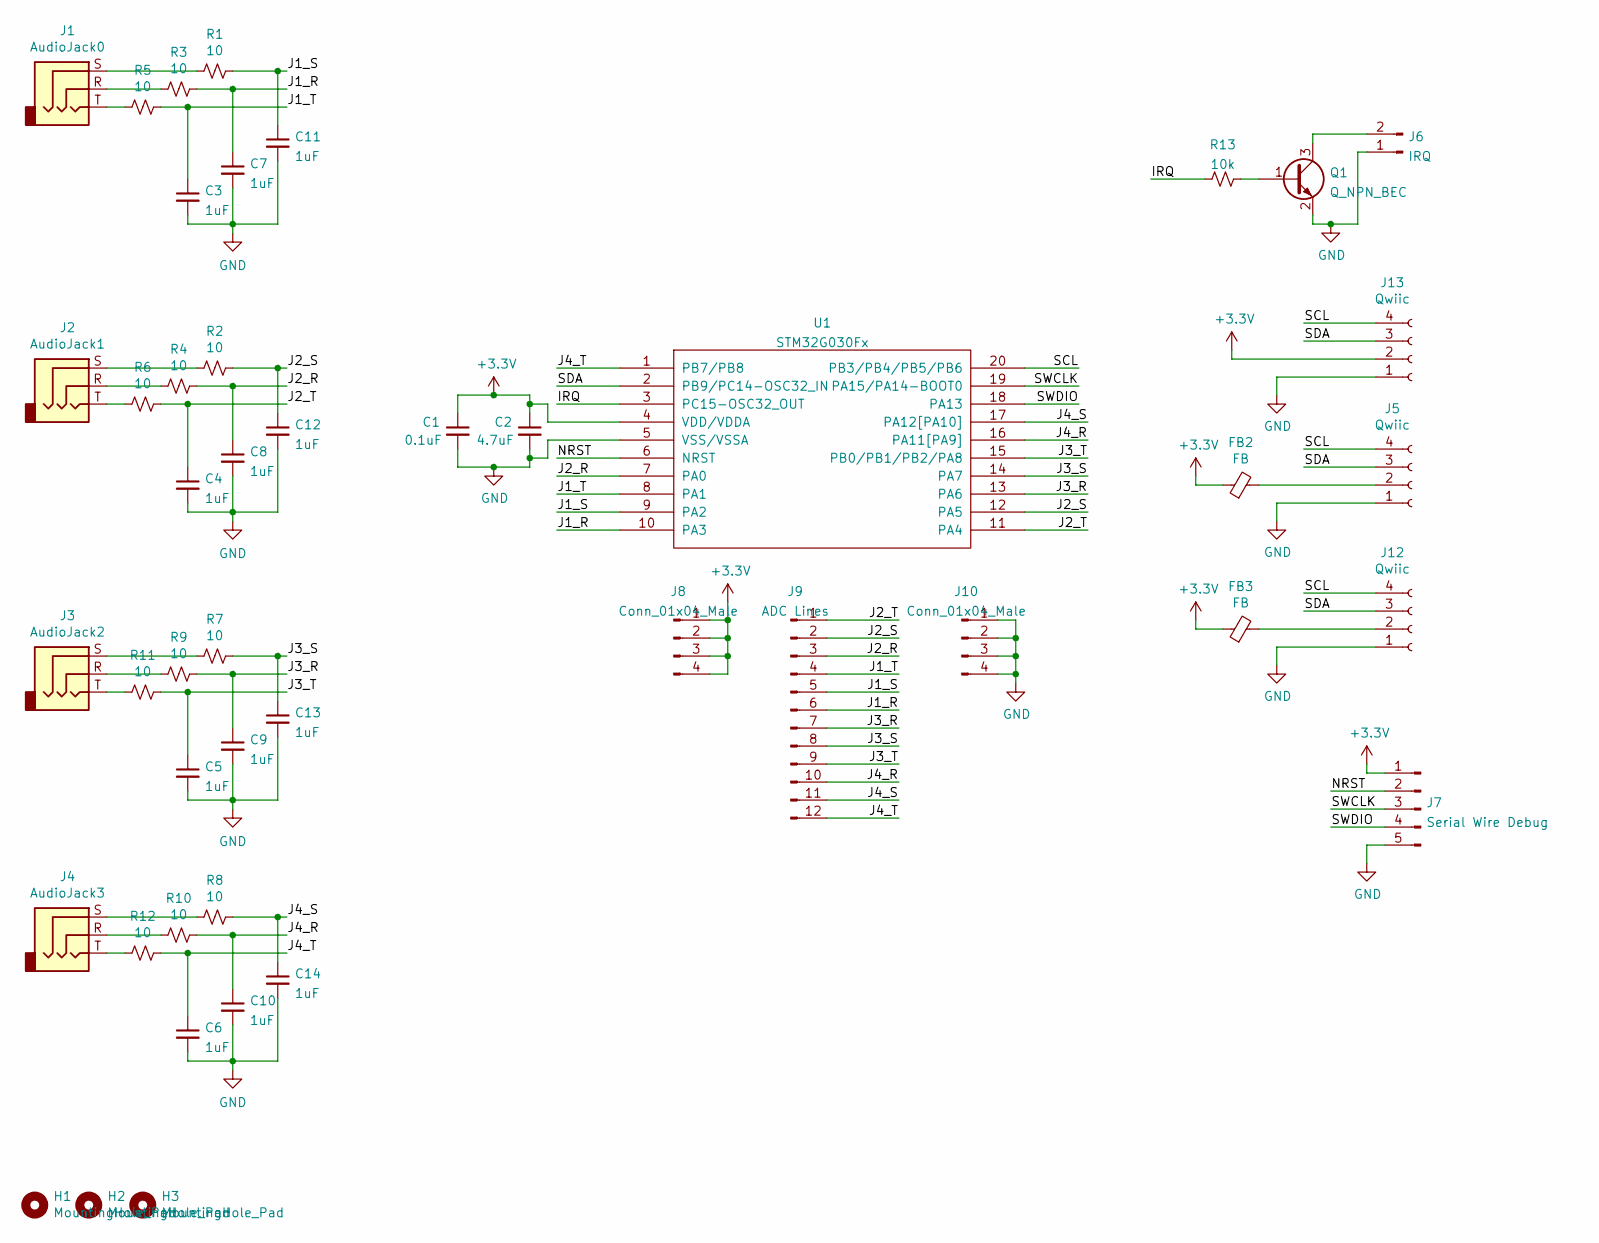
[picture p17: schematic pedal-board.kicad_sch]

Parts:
C1: 0.1uF; C_0805_2012Metric_Pad1.18x1.45mm_HandSolder
C2: 4.7uF; C_0805_2012Metric_Pad1.18x1.45mm_HandSolder
C3, C4, C5, C6, C7, C8, C9, C10, C11, C12, C13, C14: 1uF; C_0805_2012Metric_Pad1.18x1.45mm_HandSolder
FB2, FB3: FB; L_0805_2012Metric_Pad1.05x1.20mm_HandSolder
H1, H2, H3: MountingHole_Pad; MountingHole_3.2mm_M3
J1: AudioJack0; SJ-63053A
J2: AudioJack1; SJ-63053A
J3: AudioJack2; SJ-63053A
J4: AudioJack3; SJ-63053A
J5, J12: Qwiic; JST_SH_SM04B-SRSS-TB_04x1.00mm_Angled
J6: IRQ; PinHeader_1x02_P2.54mm_Vertical
J7: Serial Wire Debug; PinHeader_1x05_P2.54mm_Vertical
J8, J10: Conn_01x04_Male; PinHeader_1x04_P2.54mm_Vertical
J9: ADC Lines; PinHeader_1x12_P2.54mm_Vertical
J13: Qwiic; PinHeader_1x04_P2.54mm_Vertical
Q1: Q_NPN_BEC; SOT-23
R1, R2, R3, R4, R5, R6, R7, R8, R9, R10, R11, R12: 10; R_0805_2012Metric_Pad1.20x1.40mm_HandSolder
R13: 10k; R_0805_2012Metric_Pad1.20x1.40mm_HandSolder
U1: STM32G030Fx; TSSOP-20_4.4x6.5mm_P0.65mm

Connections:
+3V3: C1.1, C2.1, FB2.1, FB3.1, J7.1, J8.1, J8.2, J8.3, J8.4, J13.2, U1.4 (VDD/VDDA)
/IRQ: R13.1, U1.3 (PC15-OSC32_OUT)
/J1_R: C7.1, J9.6, R3.1, U1.10 (PA3)
/J1_S: C11.1, J9.5, R1.1, U1.9 (PA2)
/J1_T: C3.1, J9.4, R5.1, U1.8 (PA1)
/J2_R: C8.1, J9.3, R4.1, U1.7 (PA0)
/J2_S: C12.1, J9.2, R2.1, U1.12 (PA5)
/J2_T: C4.1, J9.1, R6.1, U1.11 (PA4)
/J3_R: C9.1, J9.7, R9.1, U1.13 (PA6)
/J3_S: C13.1, J9.8, R7.1, U1.14 (PA7)
/J3_T: C5.1, J9.9, R11.1, U1.15 (PB0/PB1/PB2/PA8)
/J4_R: C10.1, J9.10, R10.1, U1.16 (PA11[PA9])
/J4_S: C14.1, J9.11, R8.1, U1.17 (PA12[PA10])
/J4_T: C6.1, J9.12, R12.1, U1.1 (PB7/PB8)
/NRST: J7.2, U1.6 (NRST)
/SCL: J5.4, J12.4, J13.4, U1.20 (PB3/PB4/PB5/PB6)
/SDA: J5.3, J12.3, J13.3, U1.2 (PB9/PC14-OSC32_IN)
/SWCLK: J7.3, U1.19 (PA15/PA14-BOOT0)
/SWDIO: J7.4, U1.18 (PA13)
GND: C1.2, C2.2, C3.2, C4.2, C5.2, C6.2, C7.2, C8.2, C9.2, C10.2, C11.2, C12.2, C13.2, C14.2, J5.1, J6.1, J7.5, J10.1, J10.2, J10.3, J10.4, J12.1, J13.1, Q1.2 (E), U1.5 (VSS/VSSA)
unnamed: FB2.2, J5.2
unnamed: FB3.2, J12.2
unnamed: J1.R, R3.2
unnamed: J1.S, R1.2
unnamed: J1.T, R5.2
unnamed: J2.R, R4.2
unnamed: J2.S, R2.2
unnamed: J2.T, R6.2
unnamed: J3.R, R9.2
unnamed: J3.S, R7.2
unnamed: J3.T, R11.2
unnamed: J4.R, R10.2
unnamed: J4.S, R8.2
unnamed: J4.T, R12.2
unnamed: J6.2, Q1.3 (C)
unnamed: Q1.1 (B), R13.2

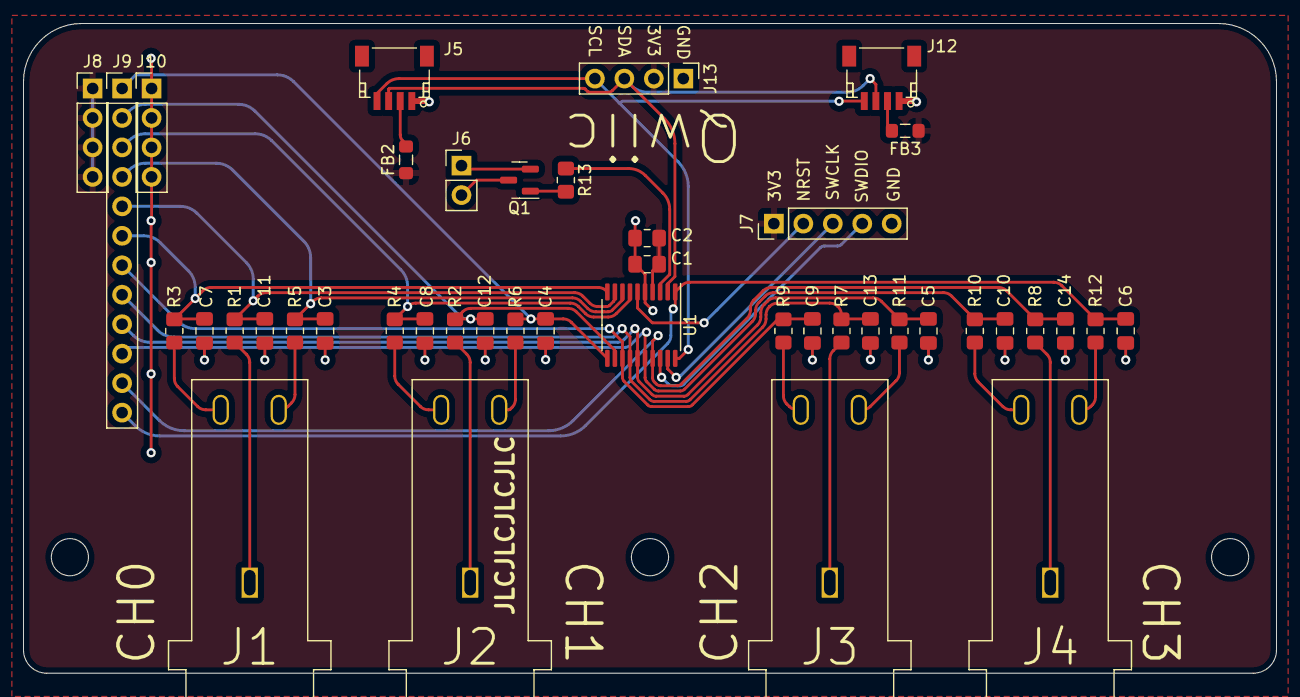
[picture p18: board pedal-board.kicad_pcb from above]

Board: 2 copper layers, 108.0 x 56.0 mm, 46 parts (0 on the bottom side), 36 nets.

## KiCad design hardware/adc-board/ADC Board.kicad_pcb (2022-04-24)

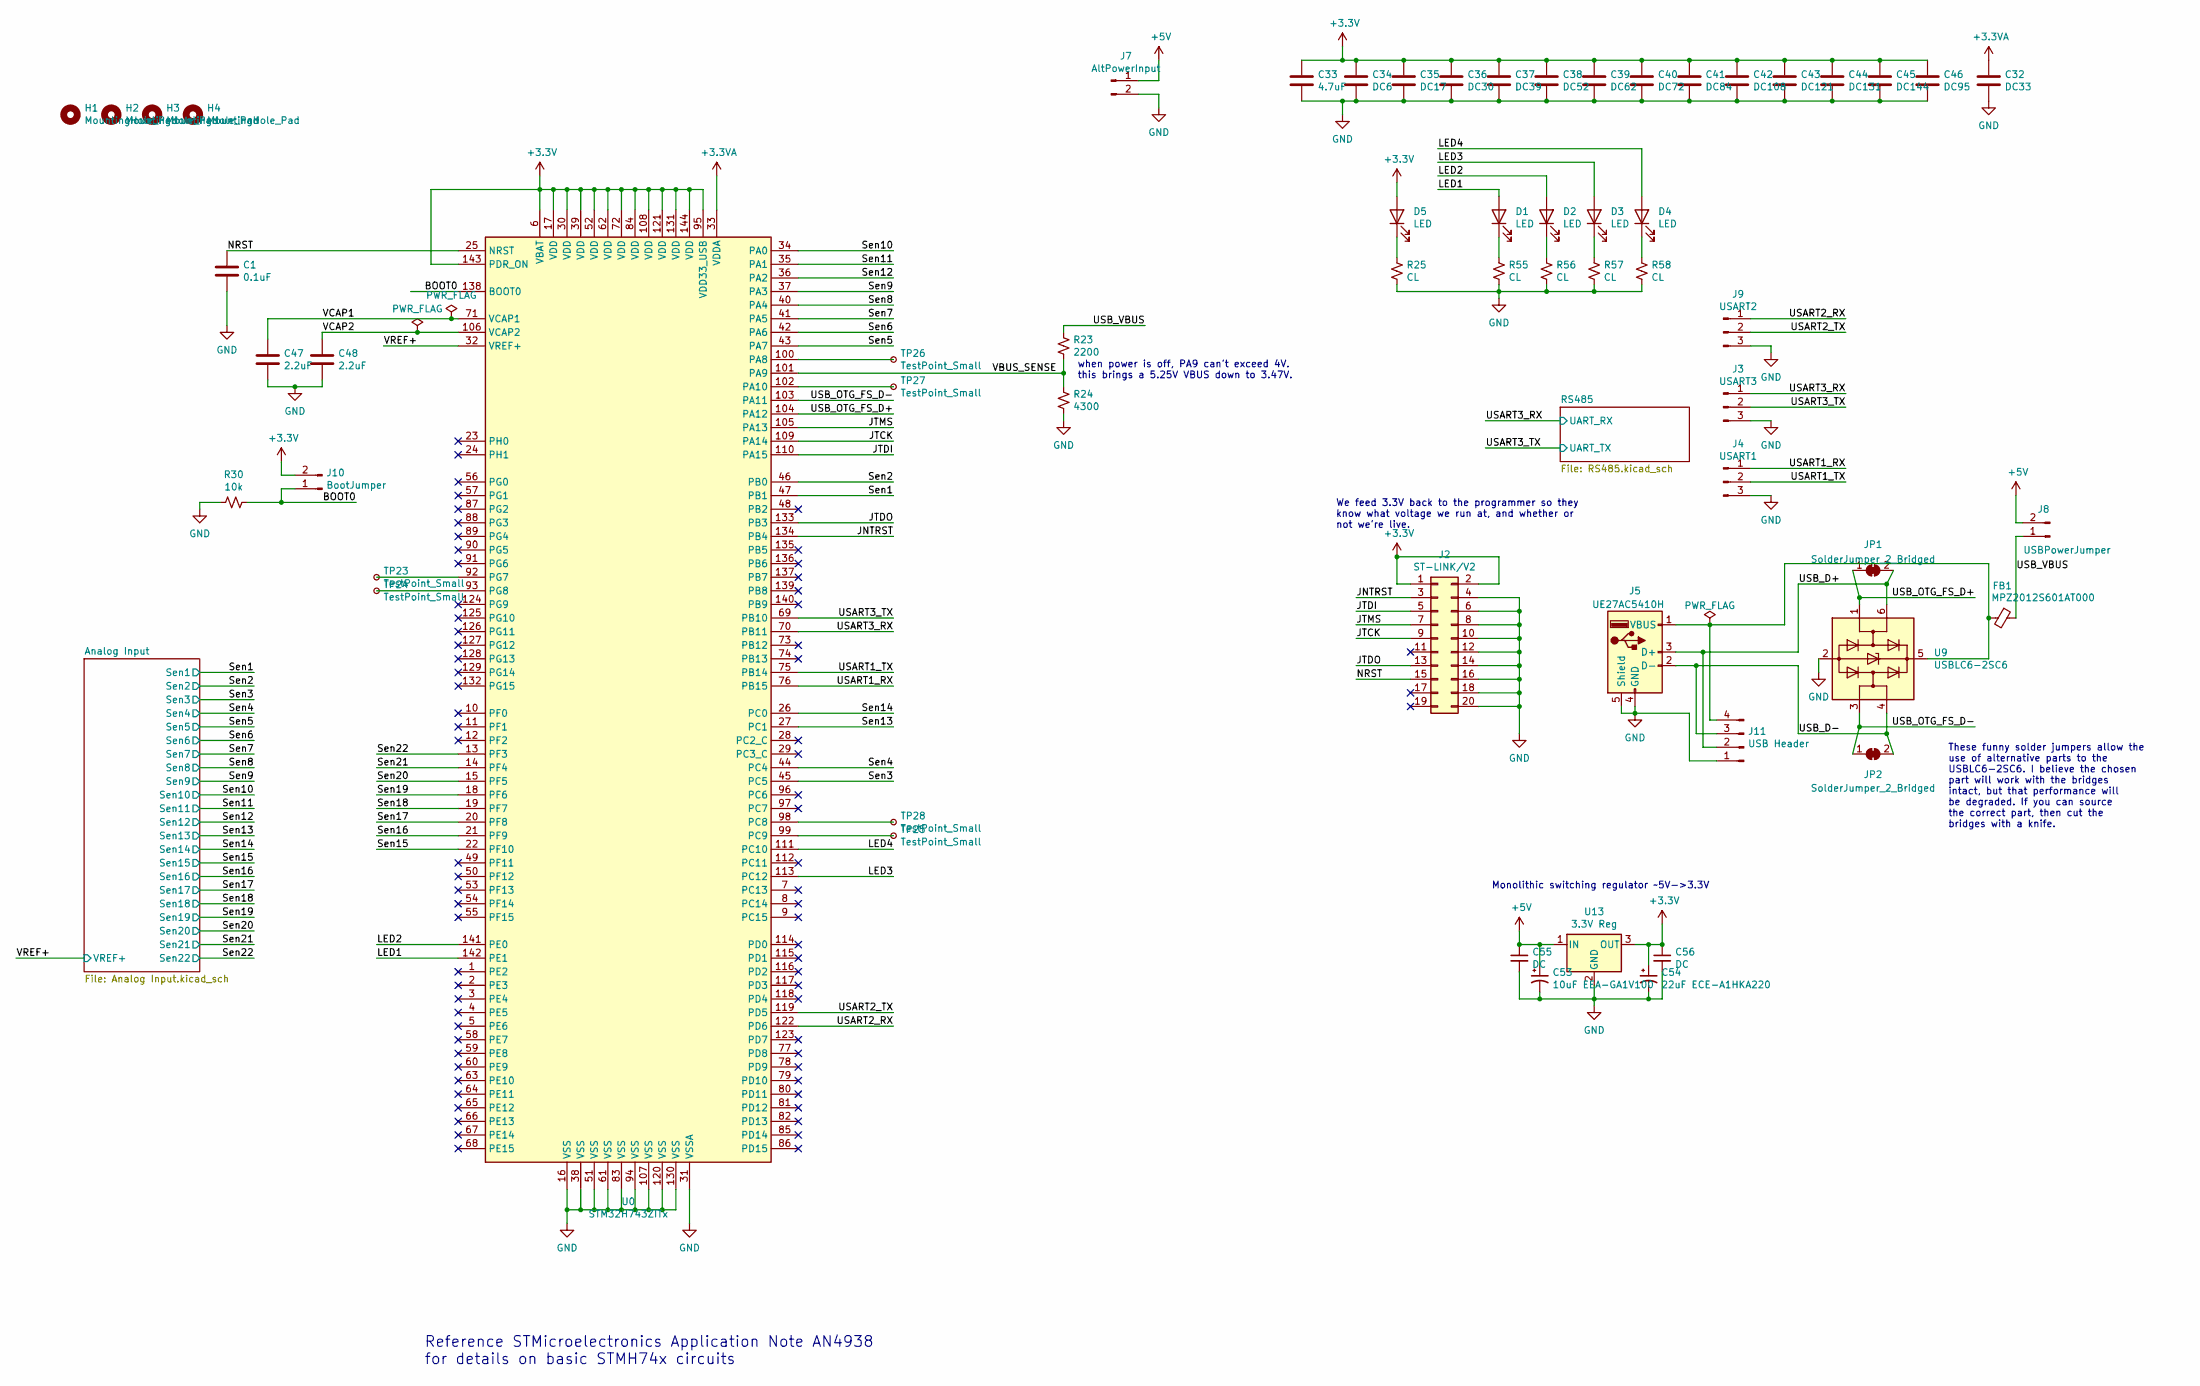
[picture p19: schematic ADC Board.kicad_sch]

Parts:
C1: 0.1uF; C_0805_2012Metric
C32: DC33; C_0805_2012Metric
C33: 4.7uF; C_0805_2012Metric
C34: DC6; C_0805_2012Metric
C35: DC17; C_0805_2012Metric
C36: DC30; C_0805_2012Metric
C37: DC39; C_0805_2012Metric
C38: DC52; C_0805_2012Metric
C39: DC62; C_0805_2012Metric
C40: DC72; C_0805_2012Metric
C41: DC84; C_0805_2012Metric
C42: DC108; C_0805_2012Metric
C43: DC121; C_0805_2012Metric
C44: DC131; C_0805_2012Metric
C45: DC144; C_0805_2012Metric
C46: DC95; C_0805_2012Metric
C47, C48: 2.2uF; C_0805_2012Metric
C53: 10uF EEA-GA1V100; CP_Elec_5x5.3
C54: 22uF ECE-A1HKA220; CP_Elec_6.3x5.3
C55, C56: DC; C_0805_2012Metric
D1, D2, D3, D4, D5: LED; LED_0805_2012Metric_Pad1.15x1.40mm_HandSolder
FB1: MPZ2012S601AT000; L_0805_2012Metric_Pad1.05x1.20mm_HandSolder
H1, H2, H3, H4: MountingHole_Pad; MountingHole_3.2mm_M3
J2: ST-LINK/V2; Pin_Header_Straight_2x10_Pitch2.54mm
J3: USART3; Pin_Header_Straight_1x03_Pitch2.54mm
J4: USART1; Pin_Header_Straight_1x03_Pitch2.54mm
J5: UE27AC5410H; USB_A_Molex_67643_Horizontal
J7: AltPowerInput; Pin_Header_Straight_1x02_Pitch2.54mm
J8: USBPowerJumper; Pin_Header_Straight_1x02_Pitch2.54mm
J9: USART2; Pin_Header_Straight_1x03_Pitch2.54mm
J10: BootJumper; Pin_Header_Straight_1x02_Pitch2.54mm
J11: USB Header; Pin_Header_Straight_1x04_Pitch2.54mm
JP1, JP2: SolderJumper_2_Bridged; SolderJumper-2_P1.3mm_Bridged_RoundedPad1.0x1.5mm
R23: 2200; R_0805_2012Metric
R24: 4300; R_0805_2012Metric
R25, R55, R56, R57, R58: CL; R_0805_2012Metric
R30: 10k; R_0805_2012Metric
TP23, TP24, TP25, TP26, TP27, TP28: TestPoint_Small; TestPoint_Pad_D1.5mm
U0: STM32H743ZITx; TQFP-144_20x20mm_P0.5mm
U9: USBLC6-2SC6; SOT-23-6_Handsoldering
U13: 3.3V Reg; TO-220-3_Vertical

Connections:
+3.3VA: C32.1, U0.33 (VDDA); also elsewhere on the board
+3V3: C33.1, C34.1, C35.1, C36.1, C37.1, C38.1, C39.1, C40.1, C41.1, C42.1, C43.1, C44.1, C45.1, C46.1, C54.1, C56.1, D5.2 (A), J2.1, J2.2, J10.2, U0.6 (VBAT), U0.17 (VDD), U0.30 (VDD), U0.39 (VDD), U0.52 (VDD), U0.62 (VDD), U0.72 (VDD), U0.84 (VDD), U0.95 (VDD33_USB), U0.108 (VDD), U0.121 (VDD), U0.131 (VDD), U0.143 (PDR_ON), U0.144 (VDD), U13.3 (OUT); also elsewhere on the board
+5V: C53.1, C55.1, J7.1, J8.2, U13.1 (IN); also elsewhere on the board
/BOOT0: J10.1, R30.1, U0.138 (BOOT0)
/JNTRST: J2.3, U0.134 (PB4)
/JTCK: J2.9, U0.109 (PA14)
/JTDI: J2.5, U0.110 (PA15)
/JTDO: J2.13, U0.133 (PB3)
/JTMS: J2.7, U0.105 (PA13)
/LED1: D1.2 (A), U0.142 (PE1)
/LED2: D2.2 (A), U0.141 (PE0)
/LED3: D3.2 (A), U0.113 (PC12)
/LED4: D4.2 (A), U0.111 (PC10)
/NRST: C1.1, J2.15, U0.25 (NRST)
/Sen1: U0.47 (PB1); also elsewhere on the board
/Sen2: U0.46 (PB0); also elsewhere on the board
/Sen3: U0.45 (PC5); also elsewhere on the board
/Sen4: U0.44 (PC4); also elsewhere on the board
/Sen5: U0.43 (PA7); also elsewhere on the board
/Sen6: U0.42 (PA6); also elsewhere on the board
/Sen7: U0.41 (PA5); also elsewhere on the board
/Sen8: U0.40 (PA4); also elsewhere on the board
/Sen9: U0.37 (PA3); also elsewhere on the board
/Sen10: U0.34 (PA0); also elsewhere on the board
/Sen11: U0.35 (PA1); also elsewhere on the board
/Sen12: U0.36 (PA2); also elsewhere on the board
/Sen13: U0.27 (PC1); also elsewhere on the board
/Sen14: U0.26 (PC0); also elsewhere on the board
/Sen15: U0.22 (PF10); also elsewhere on the board
/Sen16: U0.21 (PF9); also elsewhere on the board
/Sen17: U0.20 (PF8); also elsewhere on the board
/Sen18: U0.19 (PF7); also elsewhere on the board
/Sen19: U0.18 (PF6); also elsewhere on the board
/Sen20: U0.15 (PF5); also elsewhere on the board
/Sen21: U0.14 (PF4); also elsewhere on the board
/Sen22: U0.13 (PF3); also elsewhere on the board
/USART1_RX: J4.1, U0.76 (PB15)
/USART1_TX: J4.2, U0.75 (PB14)
/USART2_RX: J9.1, U0.122 (PD6)
/USART2_TX: J9.2, U0.119 (PD5)
/USART3_RX: J3.1, U0.70 (PB11); also elsewhere on the board
/USART3_TX: J3.2, U0.69 (PB10); also elsewhere on the board
/USB_D+: J5.3 (D+), J11.2, JP1.2 (B), U9.6 (I/O1)
/USB_D-: J5.2 (D-), J11.3, JP2.2 (B), U9.4 (I/O2)
/USB_OTG_FS_D+: JP1.1 (A), U0.104 (PA12), U9.1 (I/O1)
/USB_OTG_FS_D-: JP2.1 (A), U0.103 (PA11), U9.3 (I/O2)
/USB_VBUS: FB1.1, J8.1, R23.1
/VBUS_SENSE: R23.2, R24.1, U0.101 (PA9)
/VCAP1: C47.1, U0.71 (VCAP1)
/VCAP2: C48.1, U0.106 (VCAP2)
/VREF+: U0.32 (VREF+); also elsewhere on the board
GND: C1.2, C32.2, C33.2, C34.2, C35.2, C36.2, C37.2, C38.2, C39.2, C40.2, C41.2, C42.2, C43.2, C44.2, C45.2, C46.2, C47.2, C48.2, C53.2, C54.2, C55.2, C56.2, J2.4, J2.6, J2.8, J2.10, J2.12, J2.14, J2.16, J2.18, J2.20, J3.3, J4.3, J5.4 (GND), J5.5 (Shield), J7.2, J9.3, J11.1, R24.2, R25.2, R30.2, R55.2, R56.2, R57.2, R58.2, U0.16 (VSS), U0.31 (VSSA), U0.38 (VSS), U0.51 (VSS), U0.61 (VSS), U0.83 (VSS), U0.94 (VSS), U0.107 (VSS), U0.120 (VSS), U0.130 (VSS), U9.2 (GND), U13.2 (GND); also elsewhere on the board
unnamed: D1.1 (K), R55.1
unnamed: D2.1 (K), R56.1
unnamed: D3.1 (K), R57.1
unnamed: D4.1 (K), R58.1
unnamed: D5.1 (K), R25.1
unnamed: FB1.2, J5.1 (VBUS), J11.4, U9.5 (VBUS)
unnamed: TP23.1, U0.92 (PG7)
unnamed: TP24.1, U0.93 (PG8)
unnamed: TP25.1, U0.99 (PC9)
unnamed: TP26.1, U0.100 (PA8)
unnamed: TP27.1, U0.102 (PA10)
unnamed: TP28.1, U0.98 (PC8)

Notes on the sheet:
Monolithic switching regulator ~5V->3.3V
We feed 3.3V back to the programmer so they know what voltage we run at, and whether or not we're live.
Reference STMicroelectronics Application Note AN4938 for details on basic STMH74x circuits
These funny solder jumpers allow the use of alternative parts to the USBLC6-2SC6. I believe the chosen part will work with the bridges intact, but that performance will be degraded. If you can source the correct part, then cut the bridges with a knife.
when power is off, PA9 can't exceed 4V. this brings a 5.25V VBUS down to 3.47V.

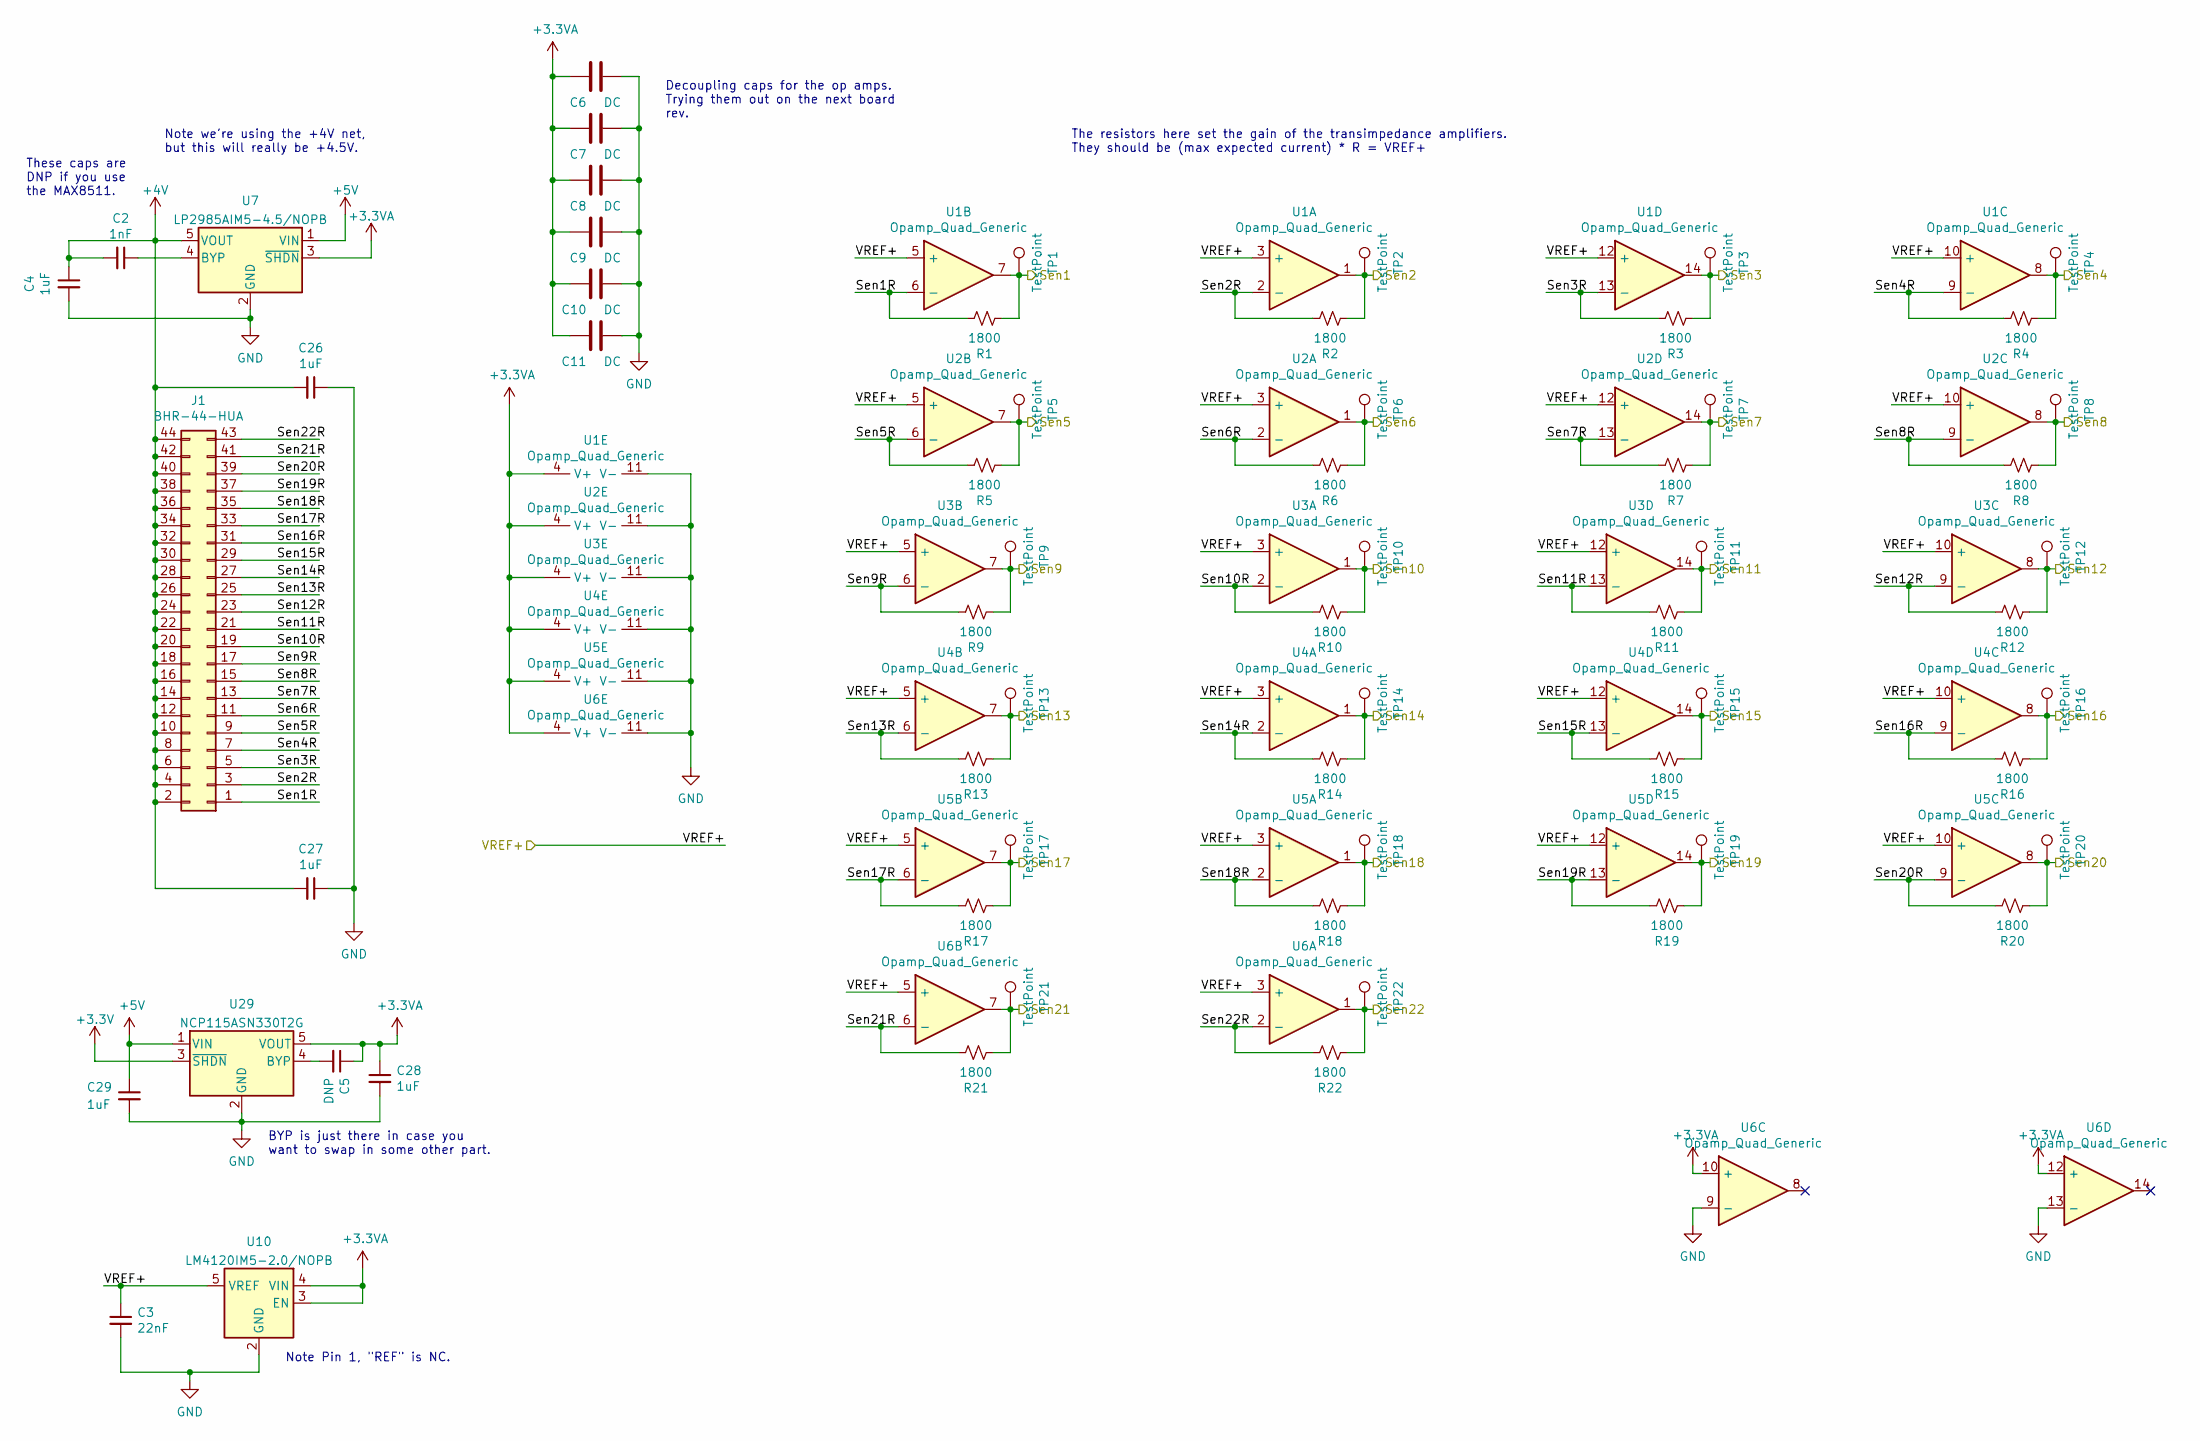
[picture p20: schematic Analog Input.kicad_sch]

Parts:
C2: 1nF; C_0805_2012Metric
C3: 22nF; C_0805_2012Metric
C4, C26, C27, C28, C29: 1uF; C_0805_2012Metric
C5: DNP; C_0805_2012Metric
C6, C7, C8, C9, C10, C11: DC; C_0805_2012Metric
J1: BHR-44-HUA; Pin_Header_Angled_2x22_Pitch2.54mm
R1, R2, R3, R4, R5, R6, R7, R8, R9, R10, R11, R12, R13, R14, R15, R16, R17, R18, R19, R20, R21, R22: 1800; R_0805_2012Metric
TP1, TP2, TP3, TP4, TP5, TP6, TP7, TP8, TP9, TP10, TP11, TP12, TP13, TP14, TP15, TP16, TP17, TP18, TP19, TP20, TP21, TP22: TestPoint; TestPoint_Pad_D1.0mm
U1, U2, U3, U4, U5, U6: Opamp_Quad_Generic; TSSOP-14_4.4x5mm_P0.65mm
U7: LP2985AIM5-4.5/NOPB; SOT-23-5
U10: LM4120IM5-2.0/NOPB; SOT-23-5
U29: NCP115ASN330T2G; SOT-23-5

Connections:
+3.3VA: C5.1, C6.1, C7.1, C8.1, C9.1, C10.1, C11.1, C28.1, U1.4 (V+), U2.4 (V+), U3.4 (V+), U4.4 (V+), U5.4 (V+), U6.4 (V+), U6.10 (+), U6.12 (+), U7.3 (~SHDN), U10.3 (EN), U10.4 (VIN), U29.5 (VOUT); also elsewhere on the board
+3V3: U29.3 (~SHDN); also elsewhere on the board
+4V: C2.2, C4.1, C26.2, C27.2, J1.2, J1.4, J1.6, J1.8, J1.10, J1.12, J1.14, J1.16, J1.18, J1.20, J1.22, J1.24, J1.26, J1.28, J1.30, J1.32, J1.34, J1.36, J1.38, J1.40, J1.42, J1.44, U7.5 (VOUT)
+5V: C29.1, U7.1 (VIN), U29.1 (VIN); also elsewhere on the board
/Analog Input/Sen1R: J1.1, R1.1, U1.6 (-)
/Analog Input/Sen2R: J1.3, R2.1, U1.2 (-)
/Analog Input/Sen3R: J1.5, R3.1, U1.13 (-)
/Analog Input/Sen4R: J1.7, R4.1, U1.9 (-)
/Analog Input/Sen5R: J1.9, R5.1, U2.6 (-)
/Analog Input/Sen6R: J1.11, R6.1, U2.2 (-)
/Analog Input/Sen7R: J1.13, R7.1, U2.13 (-)
/Analog Input/Sen8R: J1.15, R8.1, U2.9 (-)
/Analog Input/Sen9R: J1.17, R9.1, U3.6 (-)
/Analog Input/Sen10R: J1.19, R10.1, U3.2 (-)
/Analog Input/Sen11R: J1.21, R11.1, U3.13 (-)
/Analog Input/Sen12R: J1.23, R12.1, U3.9 (-)
/Analog Input/Sen13R: J1.25, R13.1, U4.6 (-)
/Analog Input/Sen14R: J1.27, R14.1, U4.2 (-)
/Analog Input/Sen15R: J1.29, R15.1, U4.13 (-)
/Analog Input/Sen16R: J1.31, R16.1, U4.9 (-)
/Analog Input/Sen17R: J1.33, R17.1, U5.6 (-)
/Analog Input/Sen18R: J1.35, R18.1, U5.2 (-)
/Analog Input/Sen19R: J1.37, R19.1, U5.13 (-)
/Analog Input/Sen20R: J1.39, R20.1, U5.9 (-)
/Analog Input/Sen21R: J1.41, R21.1, U6.6 (-)
/Analog Input/Sen22R: J1.43, R22.1, U6.2 (-)
/Sen1: R1.2, TP1.1, U1.7; also elsewhere on the board
/Sen2: R2.2, TP2.1, U1.1; also elsewhere on the board
/Sen3: R3.2, TP3.1, U1.14; also elsewhere on the board
/Sen4: R4.2, TP4.1, U1.8; also elsewhere on the board
/Sen5: R5.2, TP5.1, U2.7; also elsewhere on the board
/Sen6: R6.2, TP6.1, U2.1; also elsewhere on the board
/Sen7: R7.2, TP7.1, U2.14; also elsewhere on the board
/Sen8: R8.2, TP8.1, U2.8; also elsewhere on the board
/Sen9: R9.2, TP9.1, U3.7; also elsewhere on the board
/Sen10: R10.2, TP10.1, U3.1; also elsewhere on the board
/Sen11: R11.2, TP11.1, U3.14; also elsewhere on the board
/Sen12: R12.2, TP12.1, U3.8; also elsewhere on the board
/Sen13: R13.2, TP13.1, U4.7; also elsewhere on the board
/Sen14: R14.2, TP14.1, U4.1; also elsewhere on the board
/Sen15: R15.2, TP15.1, U4.14; also elsewhere on the board
/Sen16: R16.2, TP16.1, U4.8; also elsewhere on the board
/Sen17: R17.2, TP17.1, U5.7; also elsewhere on the board
/Sen18: R18.2, TP18.1, U5.1; also elsewhere on the board
/Sen19: R19.2, TP19.1, U5.14; also elsewhere on the board
/Sen20: R20.2, TP20.1, U5.8; also elsewhere on the board
/Sen21: R21.2, TP21.1, U6.7; also elsewhere on the board
/Sen22: R22.2, TP22.1, U6.1; also elsewhere on the board
/VREF+: C3.1, U1.3 (+), U1.5 (+), U1.10 (+), U1.12 (+), U2.3 (+), U2.5 (+), U2.10 (+), U2.12 (+), U3.3 (+), U3.5 (+), U3.10 (+), U3.12 (+), U4.3 (+), U4.5 (+), U4.10 (+), U4.12 (+), U5.3 (+), U5.5 (+), U5.10 (+), U5.12 (+), U6.3 (+), U6.5 (+), U10.5 (VREF); also elsewhere on the board
GND: C3.2, C4.2, C6.2, C7.2, C8.2, C9.2, C10.2, C11.2, C26.1, C27.1, C28.2, C29.2, U1.11 (V-), U2.11 (V-), U3.11 (V-), U4.11 (V-), U5.11 (V-), U6.9 (-), U6.11 (V-), U6.13 (-), U7.2 (GND), U10.2 (GND), U29.2 (GND); also elsewhere on the board
unnamed: C2.1, U7.4 (BYP)
unnamed: C5.2, U29.4 (BYP)

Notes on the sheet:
The resistors here set the gain of the transimpedance amplifiers. They should be (max expected current) * R =~{} VREF+
Note Pin 1, "REF" is NC.
Note we're using the +4V net, but this will really be +4.5V.
These caps are DNP if you use the MAX8511.
Decoupling caps for the op amps. Trying them out on the next board rev.
BYP is just there in case you want to swap in some other part.

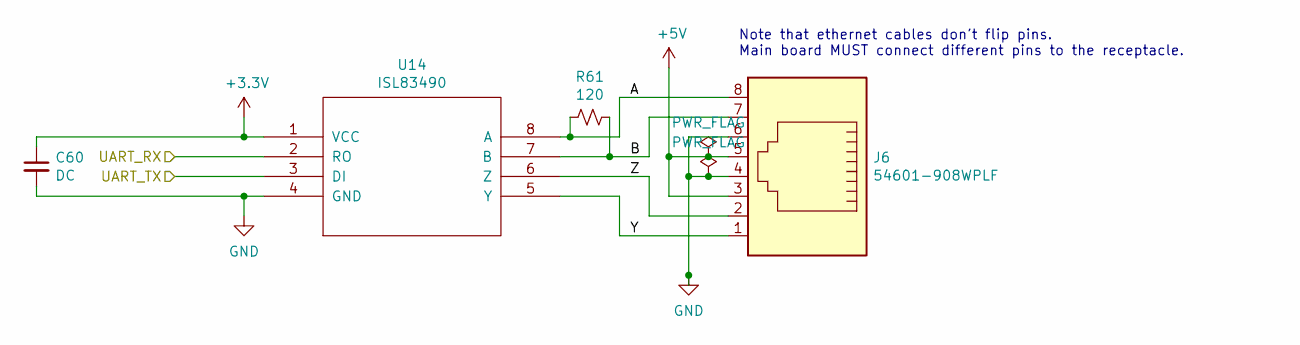
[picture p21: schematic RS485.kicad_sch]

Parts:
C60: DC; C_0805_2012Metric
J6: 54601-908WPLF; RJ45_8
R61: 120; R_0805_2012Metric
U14: ISL83490; SOP-8_3.9x4.9mm_P1.27mm

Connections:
+3V3: C60.1, U14.1 (VCC); also elsewhere on the board
+5V: J6.3, J6.5; also elsewhere on the board
/RS485/A: J6.8, R61.2, U14.8 (A)
/RS485/B: J6.7, R61.1, U14.7 (B)
/RS485/Y: J6.1, U14.5 (Y)
/RS485/Z: J6.2, U14.6 (Z)
/USART3_RX: U14.2 (RO); also elsewhere on the board
/USART3_TX: U14.3 (DI); also elsewhere on the board
GND: C60.2, J6.4, J6.6, U14.4 (GND); also elsewhere on the board

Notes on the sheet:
Note that ethernet cables don't flip pins. Main board MUST connect different pins to the receptacle.

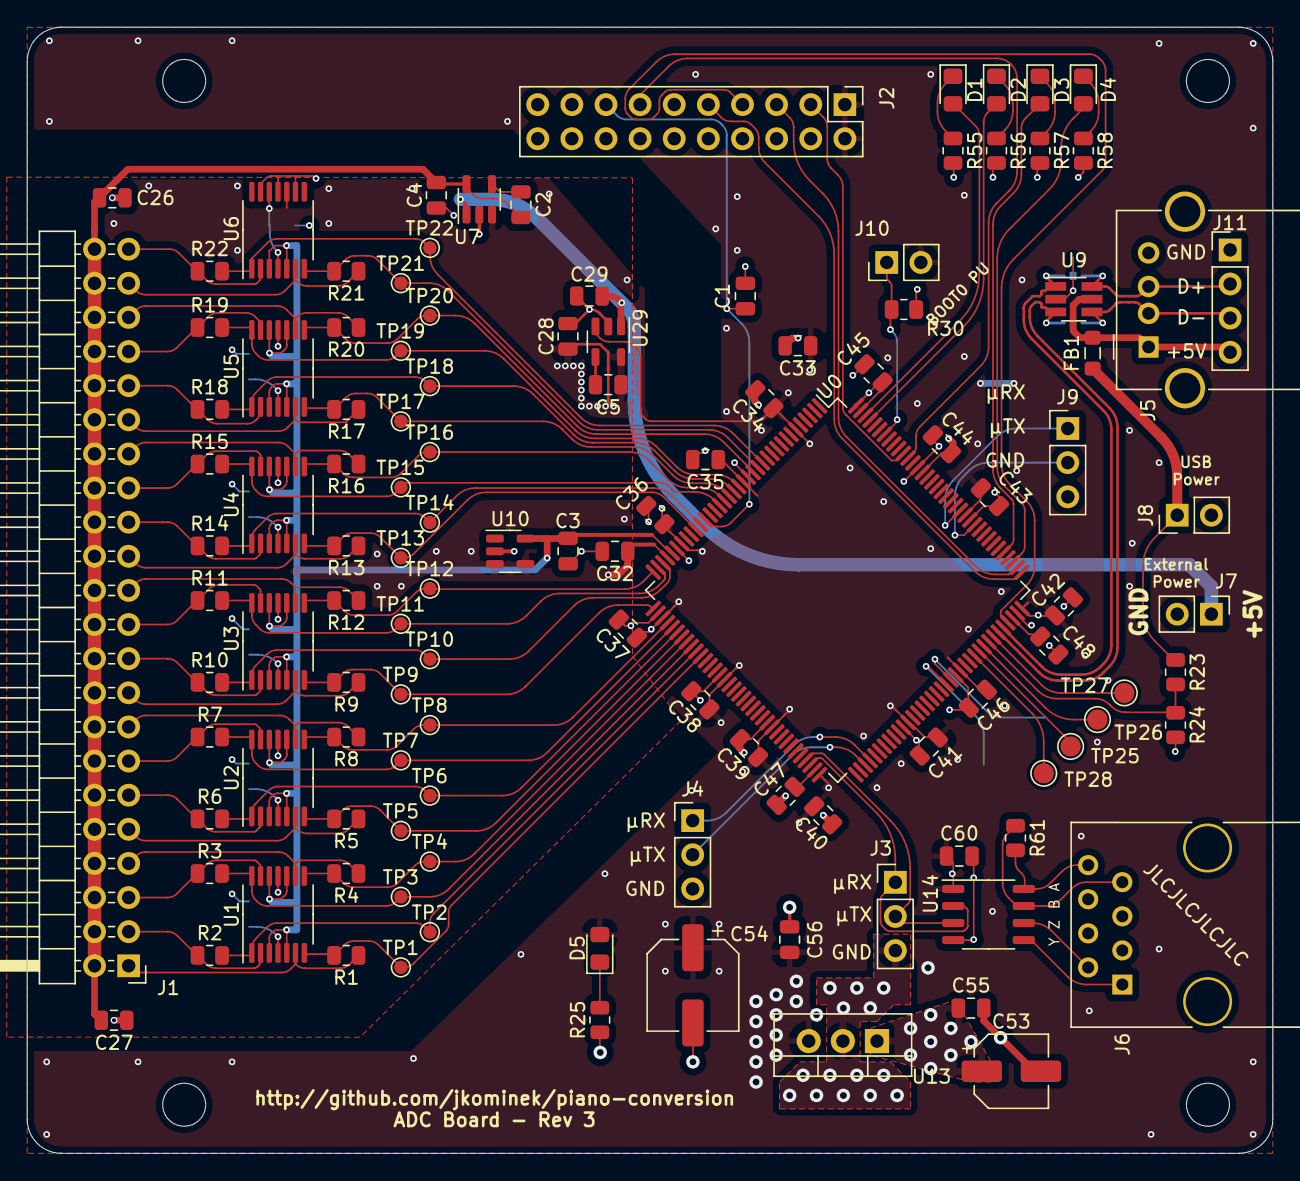
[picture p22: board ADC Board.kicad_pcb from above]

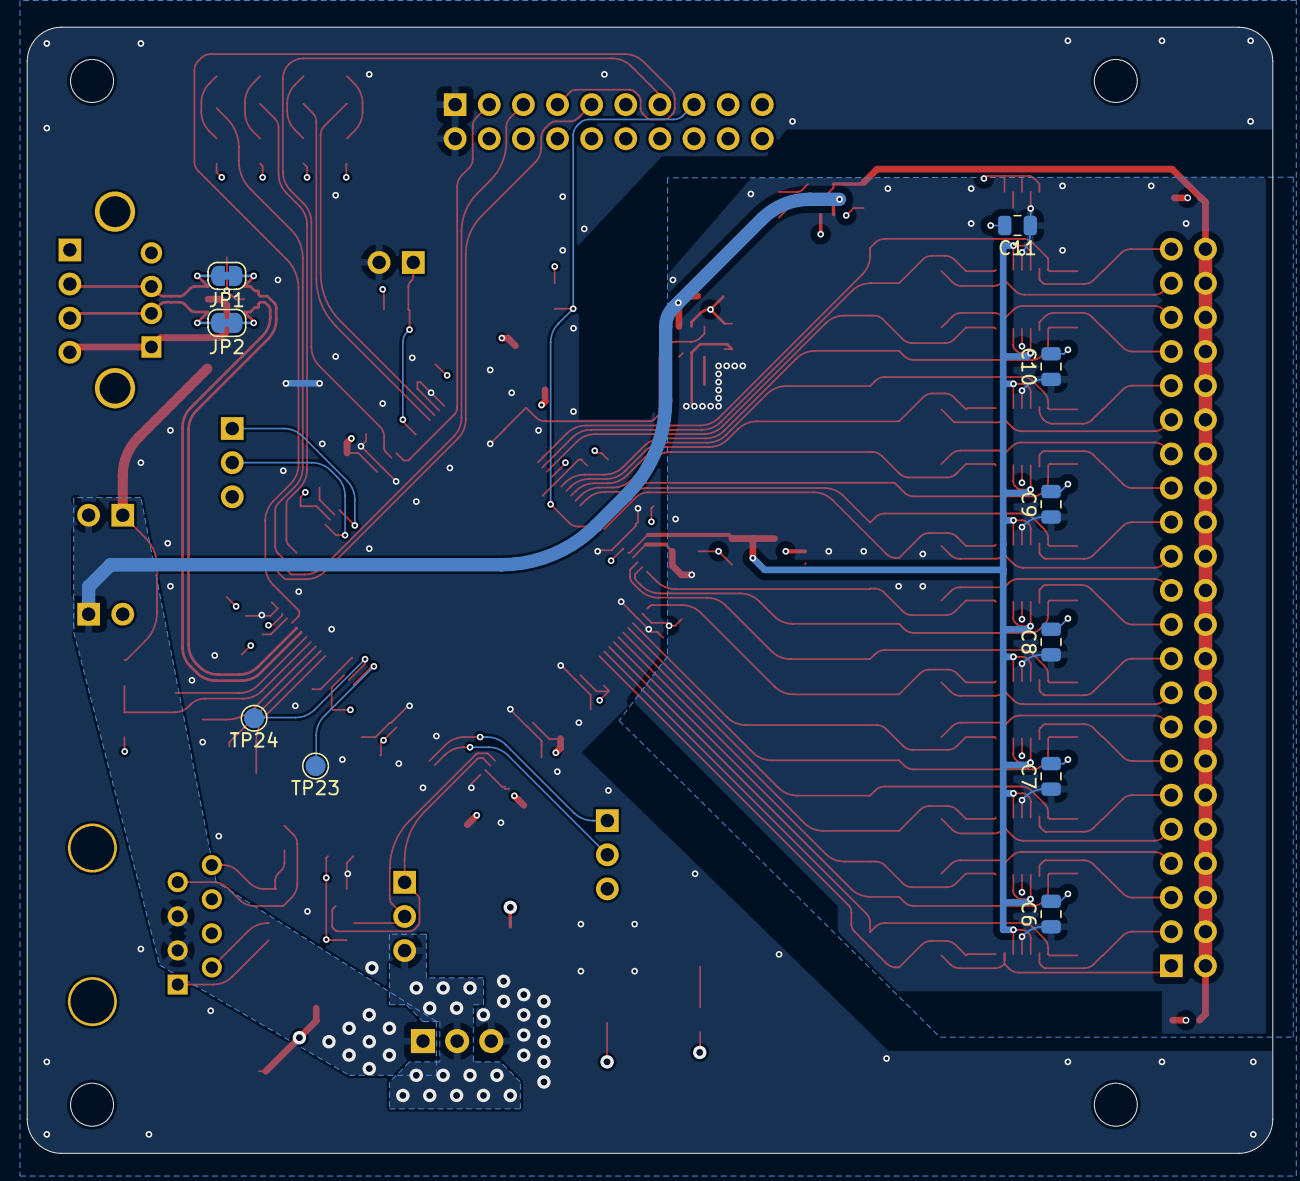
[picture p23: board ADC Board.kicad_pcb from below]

Board: 4 copper layers, 92.7 x 83.8 mm, 132 parts (10 on the bottom side), 93 nets.

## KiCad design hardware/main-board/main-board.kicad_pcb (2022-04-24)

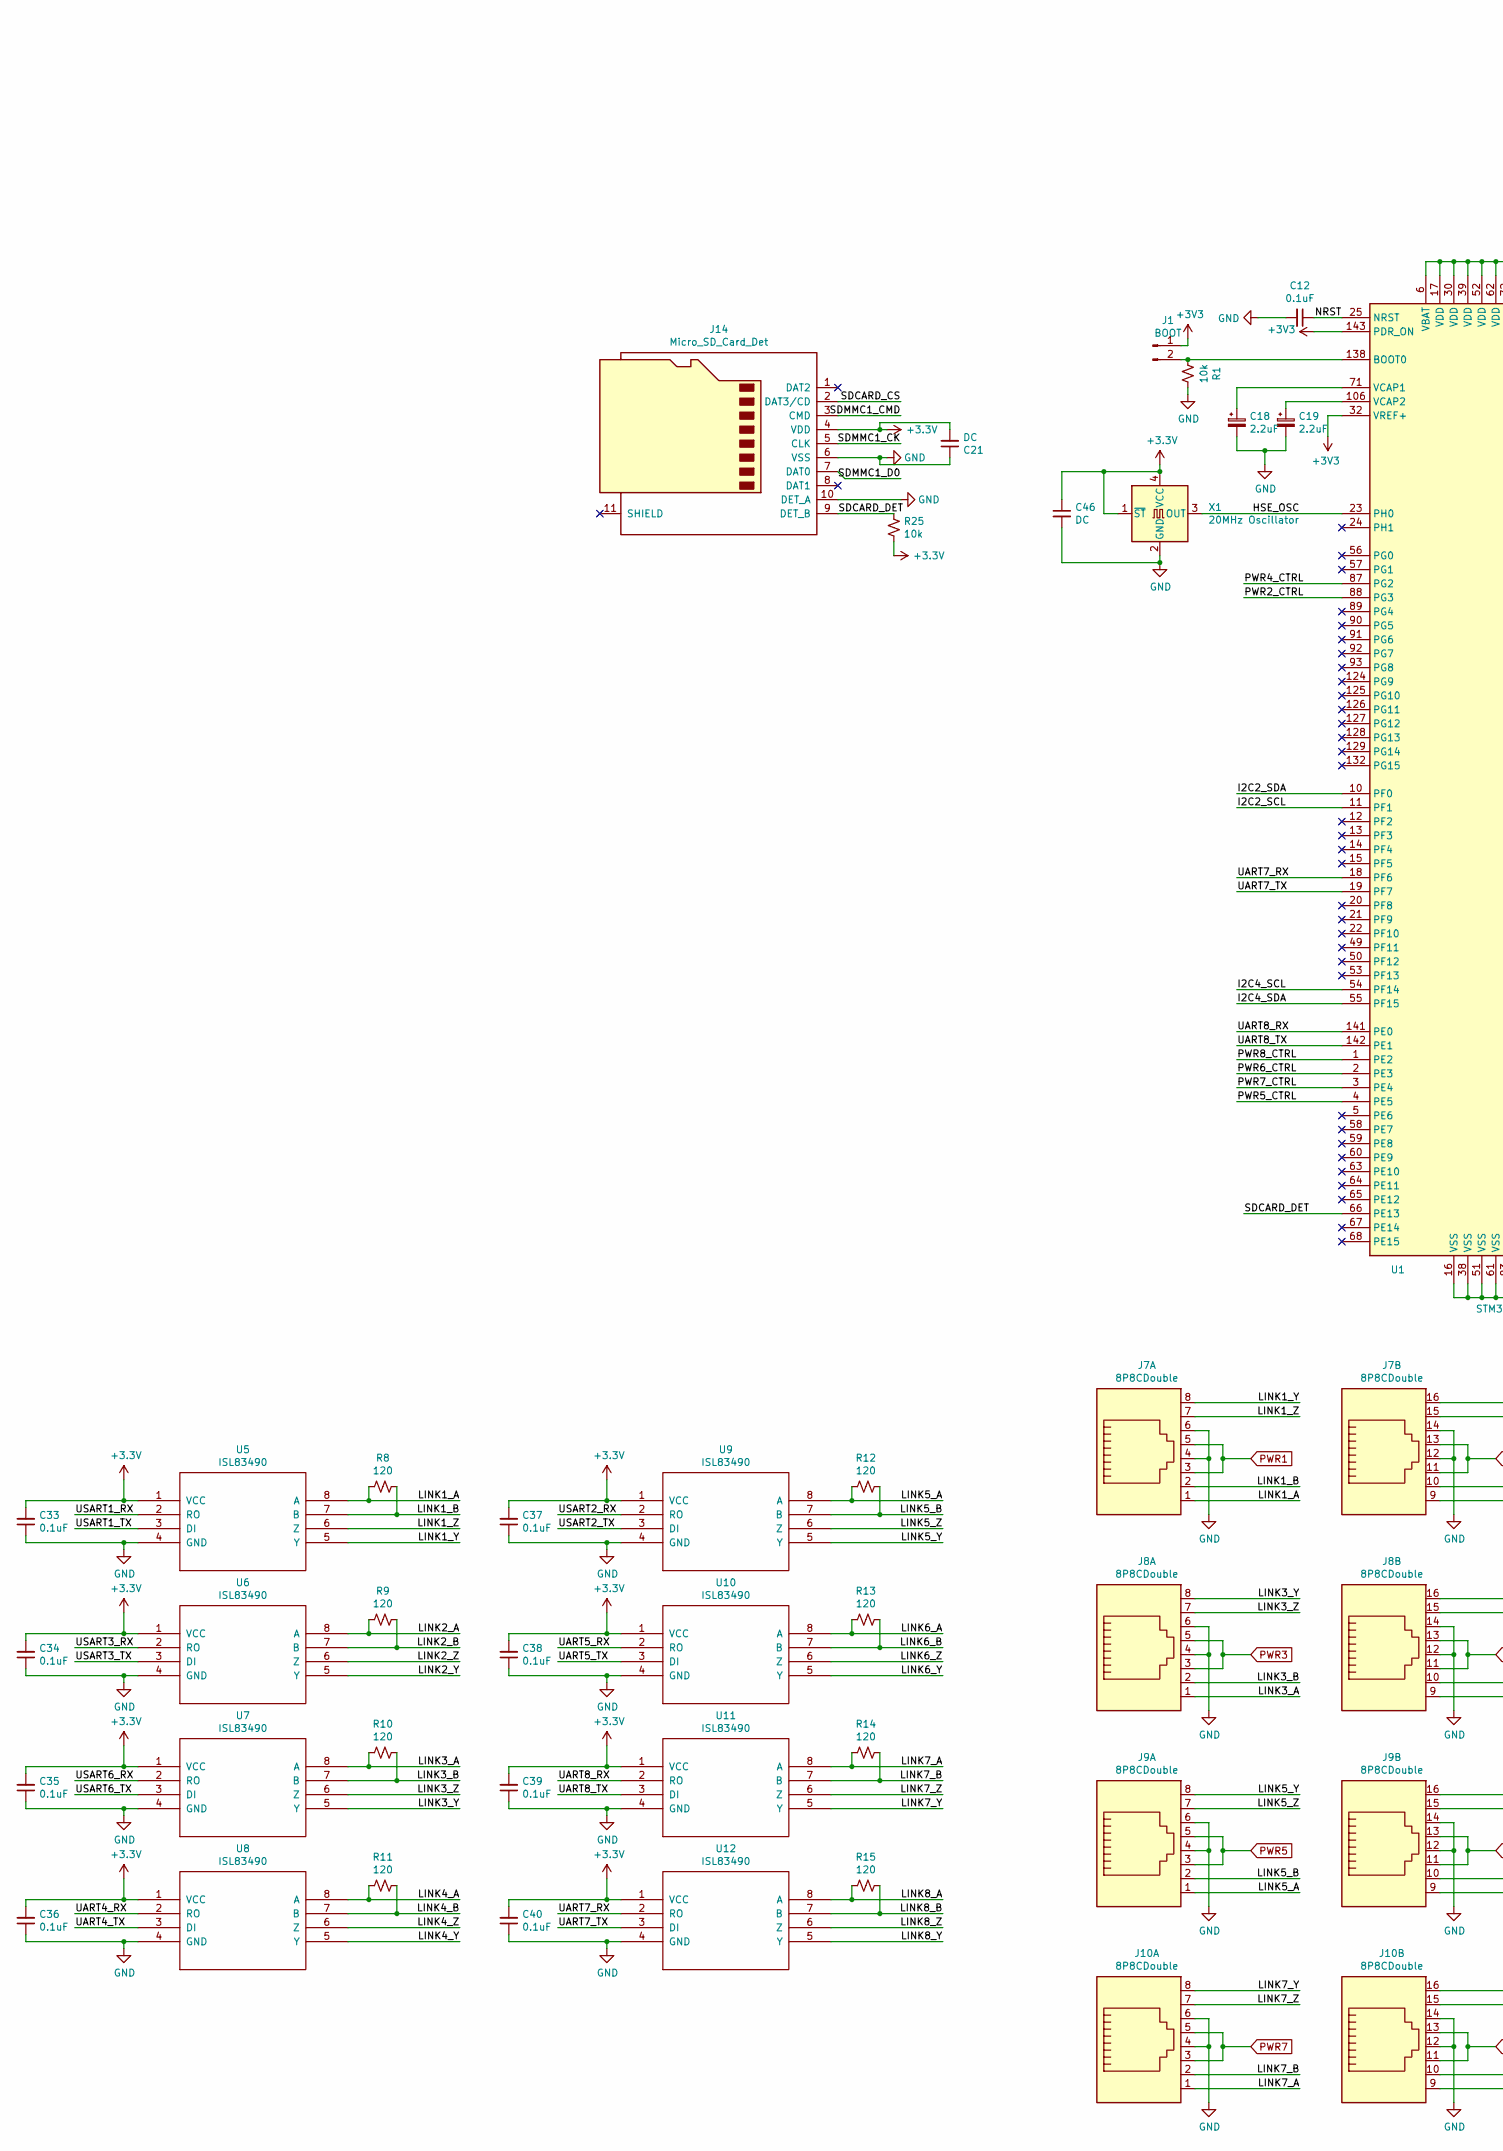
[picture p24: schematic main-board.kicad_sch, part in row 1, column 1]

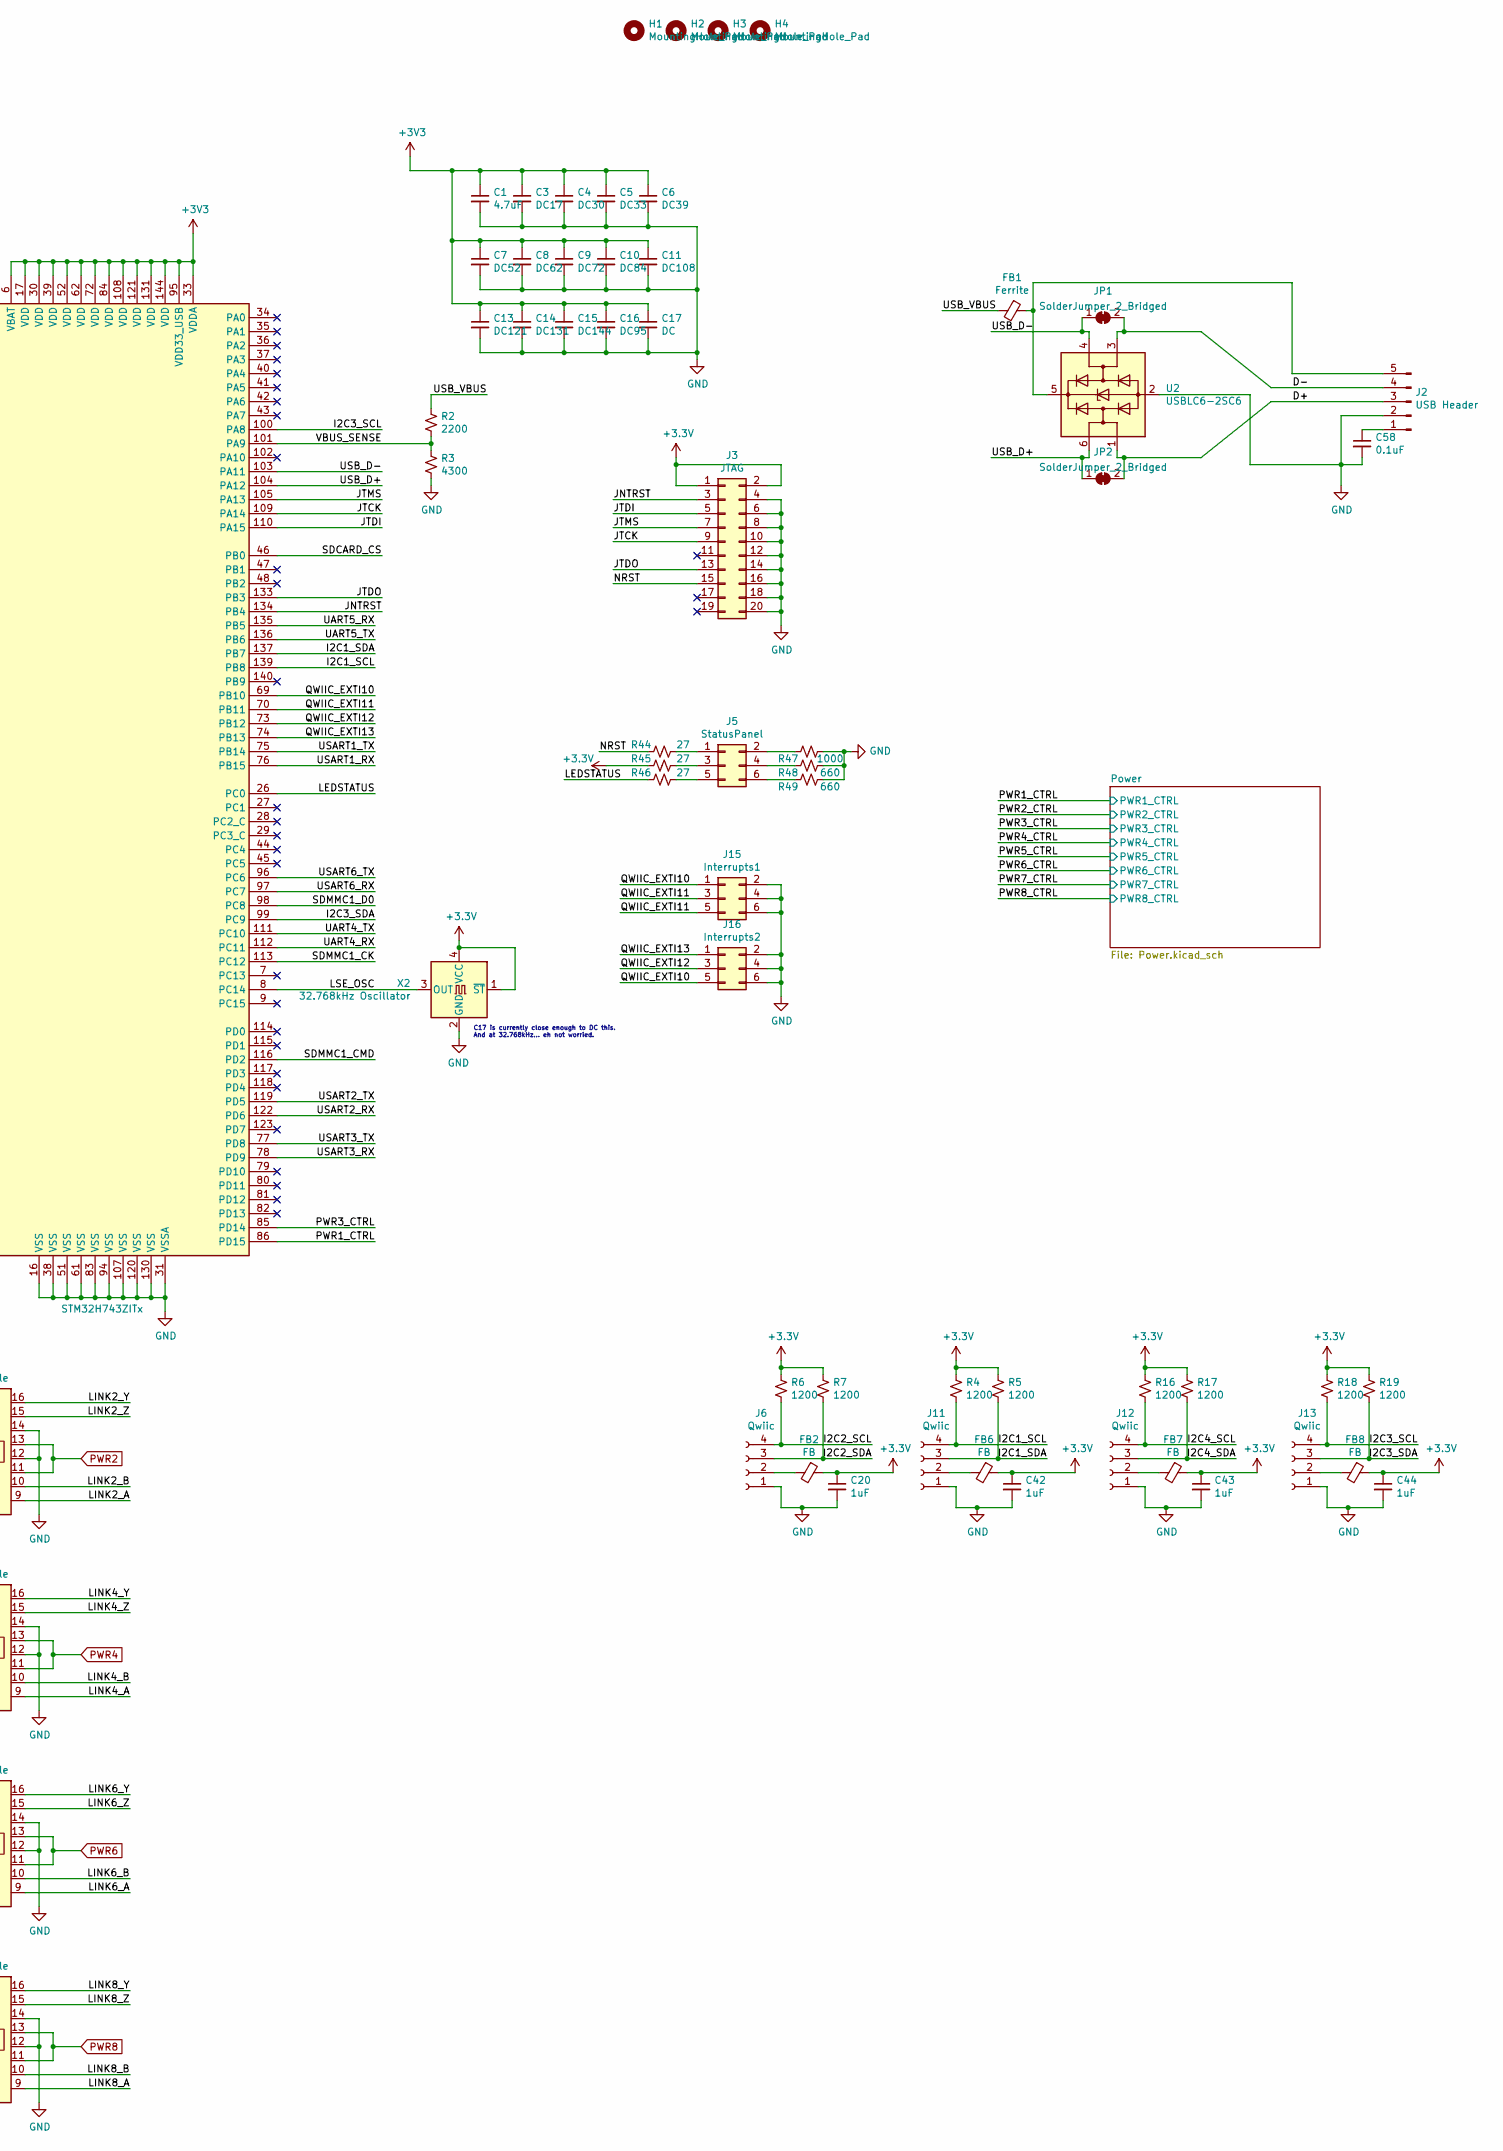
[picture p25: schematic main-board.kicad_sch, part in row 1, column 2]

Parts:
C1: 4.7uF; C_0805_2012Metric
C3: DC17; C_0805_2012Metric
C4: DC30; C_0805_2012Metric
C5: DC33; C_0805_2012Metric
C6: DC39; C_0805_2012Metric
C7: DC52; C_0805_2012Metric
C8: DC62; C_0805_2012Metric
C9: DC72; C_0805_2012Metric
C10: DC84; C_0805_2012Metric
C11: DC108; C_0805_2012Metric
C12, C33, C34, C35, C36, C37, C38, C39, C40, C58: 0.1uF; C_0805_2012Metric
C13: DC121; C_0805_2012Metric
C14: DC131; C_0805_2012Metric
C15: DC144; C_0805_2012Metric
C16: DC95; C_0805_2012Metric
C17, C21, C46: DC; C_0805_2012Metric
C18, C19: 2.2uF; C_0805_2012Metric
C20, C42, C43, C44: 1uF; C_0805_2012Metric
FB1: Ferrite; L_0805_2012Metric_Pad1.05x1.20mm_HandSolder
FB2, FB6, FB7, FB8: FB; L_0805_2012Metric_Pad1.05x1.20mm_HandSolder
H1, H2, H3, H4: MountingHole_Pad; MountingHole_3.2mm_M3
J1: BOOT; Pin_Header_Straight_1x02_Pitch2.54mm
J2: USB Header; Pin_Header_Straight_1x05_Pitch2.54mm
J3: JTAG; Pin_Header_Straight_2x10_Pitch2.54mm
J5: StatusPanel; Pin_Header_Straight_2x03_Pitch2.54mm
J6, J11, J12, J13: Qwiic; JST_SH_SM04B-SRSS-TB_04x1.00mm_Angled
J7, J8, J9, J10: 8P8CDouble; RJ45_DOUBLE
J14: Micro_SD_Card_Det; 114-00841-68
J15: Interrupts1; Pin_Header_Straight_2x03_Pitch2.54mm
J16: Interrupts2; Pin_Header_Straight_2x03_Pitch2.54mm
JP1, JP2: SolderJumper_2_Bridged; SolderJumper-2_P1.3mm_Bridged_RoundedPad1.0x1.5mm
R1, R25: 10k; R_0805
R2: 2200; R_0805
R3: 4300; R_0805
R4, R5, R6, R7, R16, R17, R18, R19: 1200; R_0805
R8, R9, R10, R11, R12, R13, R14, R15: 120; R_0805
R44, R45, R46: 27; R_0805
R47: 1000; R_0805
R48, R49: 660; R_0805
U1: STM32H743ZITx; LQFP-144_20x20mm_Pitch0.5mm
U2: USBLC6-2SC6; SOT-23-6_Handsoldering
U5, U6, U7, U8, U9, U10, U11, U12: ISL83490; SOIC-8_3.9x4.9mm_Pitch1.27mm
X1: 20MHz Oscillator; Oscillator_SMD_SeikoEpson_SG8002CE-4pin_3.2x2.5mm_HandSolde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
X2: 32.768kHz Oscillator; Oscillator_SMD_SeikoEpson_SG8002CE-4pin_3.2x2.5mm_HandSolde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

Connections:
/D+: J2.3, JP2.2 (B), U2.1 (I/O1)
/D-: J2.4, JP1.2 (B), U2.3 (I/O2)
/HSE_OSC: U1.23 (PH0), X1.3 (OUT)
/I2C1_SCL: J11.4, R4.2, U1.139 (PB8)
/I2C1_SDA: J11.3, R5.2, U1.137 (PB7)
/I2C2_SCL: J6.4, R6.2, U1.11 (PF1)
/I2C2_SDA: J6.3, R7.2, U1.10 (PF0)
/I2C3_SCL: J13.4, R18.2, U1.100 (PA8)
/I2C3_SDA: J13.3, R19.2, U1.99 (PC9)
/I2C4_SCL: J12.4, R16.2, U1.54 (PF14)
/I2C4_SDA: J12.3, R17.2, U1.55 (PF15)
/JNTRST: J3.3, U1.134 (PB4)
/JTCK: J3.9, U1.109 (PA14)
/JTDI: J3.5, U1.110 (PA15)
/JTDO: J3.13, U1.133 (PB3)
/JTMS: J3.7, U1.105 (PA13)
/LEDSTATUS: R46.2, U1.26 (PC0)
/LINK1_A: J7.1, R8.2, U5.8 (A)
/LINK1_B: J7.2, R8.1, U5.7 (B)
/LINK1_Y: J7.8, U5.5 (Y)
/LINK1_Z: J7.7, U5.6 (Z)
/LINK2_A: J7.9, R9.2, U6.8 (A)
/LINK2_B: J7.10, R9.1, U6.7 (B)
/LINK2_Y: J7.16, U6.5 (Y)
/LINK2_Z: J7.15, U6.6 (Z)
/LINK3_A: J8.1, R10.2, U7.8 (A)
/LINK3_B: J8.2, R10.1, U7.7 (B)
/LINK3_Y: J8.8, U7.5 (Y)
/LINK3_Z: J8.7, U7.6 (Z)
/LINK4_A: J8.9, R11.2, U8.8 (A)
/LINK4_B: J8.10, R11.1, U8.7 (B)
/LINK4_Y: J8.16, U8.5 (Y)
/LINK4_Z: J8.15, U8.6 (Z)
/LINK5_A: J9.1, R12.2, U9.8 (A)
/LINK5_B: J9.2, R12.1, U9.7 (B)
/LINK5_Y: J9.8, U9.5 (Y)
/LINK5_Z: J9.7, U9.6 (Z)
/LINK6_A: J9.9, R13.2, U10.8 (A)
/LINK6_B: J9.10, R13.1, U10.7 (B)
/LINK6_Y: J9.16, U10.5 (Y)
/LINK6_Z: J9.15, U10.6 (Z)
/LINK7_A: J10.1, R14.2, U11.8 (A)
/LINK7_B: J10.2, R14.1, U11.7 (B)
/LINK7_Y: J10.8, U11.5 (Y)
/LINK7_Z: J10.7, U11.6 (Z)
/LINK8_A: J10.9, R15.2, U12.8 (A)
/LINK8_B: J10.10, R15.1, U12.7 (B)
/LINK8_Y: J10.16, U12.5 (Y)
/LINK8_Z: J10.15, U12.6 (Z)
/LSE_OSC: U1.8 (PC14), X2.3 (OUT)
/NRST: C12.1, J3.15, R44.2, U1.25 (NRST)
/PWR1_CTRL: U1.86 (PD15); also elsewhere on the board
/PWR2_CTRL: U1.88 (PG3); also elsewhere on the board
/PWR3_CTRL: U1.85 (PD14); also elsewhere on the board
/PWR4_CTRL: U1.87 (PG2); also elsewhere on the board
/PWR5_CTRL: U1.4 (PE5); also elsewhere on the board
/PWR6_CTRL: U1.2 (PE3); also elsewhere on the board
/PWR7_CTRL: U1.3 (PE4); also elsewhere on the board
/PWR8_CTRL: U1.1 (PE2); also elsewhere on the board
/QWIIC_EXTI10: J15.1, J16.5, U1.69 (PB10)
/QWIIC_EXTI11: J15.3, J15.5, U1.70 (PB11)
/QWIIC_EXTI12: J16.3, U1.73 (PB12)
/QWIIC_EXTI13: J16.1, U1.74 (PB13)
/SDCARD_CS: J14.2 (DAT3/CD), U1.46 (PB0)
/SDCARD_DET: J14.9 (DET_B), R25.2, U1.66 (PE13)
/SDMMC1_CK: J14.5 (CLK), U1.113 (PC12)
/SDMMC1_CMD: J14.3 (CMD), U1.116 (PD2)
/SDMMC1_D0: J14.7 (DAT0), U1.98 (PC8)
/UART4_RX: U1.112 (PC11), U8.2 (RO)
/UART4_TX: U1.111 (PC10), U8.3 (DI)
/UART5_RX: U1.135 (PB5), U10.2 (RO)
/UART5_TX: U1.136 (PB6), U10.3 (DI)
/UART7_RX: U1.18 (PF6), U12.2 (RO)
/UART7_TX: U1.19 (PF7), U12.3 (DI)
/UART8_RX: U1.141 (PE0), U11.2 (RO)
/UART8_TX: U1.142 (PE1), U11.3 (DI)
/USART1_RX: U1.76 (PB15), U5.2 (RO)
/USART1_TX: U1.75 (PB14), U5.3 (DI)
/USART2_RX: U1.122 (PD6), U9.2 (RO)
/USART2_TX: U1.119 (PD5), U9.3 (DI)
/USART3_RX: U1.78 (PD9), U6.2 (RO)
/USART3_TX: U1.77 (PD8), U6.3 (DI)
/USART6_RX: U1.97 (PC7), U7.2 (RO)
/USART6_TX: U1.96 (PC6), U7.3 (DI)
/USB_D+: JP2.1 (A), U1.104 (PA12), U2.6 (I/O1)
/USB_D-: JP1.1 (A), U1.103 (PA11), U2.4 (I/O2)
/USB_VBUS: FB1.2, R2.1
/VBUS_SENSE: R2.2, R3.1, U1.101 (PA9)
GND: C1.2, C3.2, C4.2, C5.2, C6.2, C7.2, C8.2, C9.2, C10.2, C11.2, C12.2, C13.2, C14.2, C15.2, C16.2, C17.2, C18.2, C19.2, C20.2, C21.1, C33.1, C34.1, C35.1, C36.1, C37.1, C38.1, C39.1, C40.1, C42.2, C43.2, C44.2, C46.2, C58.2, J2.2, J3.4, J3.6, J3.8, J3.10, J3.12, J3.14, J3.16, J3.18, J3.20, J6.1, J7.4, J7.6, J7.12, J7.14, J8.4, J8.6, J8.12, J8.14, J9.4, J9.6, J9.12, J9.14, J10.4, J10.6, J10.12, J10.14, J11.1, J12.1, J13.1, J14.6 (VSS), J14.10 (DET_A), J15.2, J15.4, J15.6, J16.2, J16.4, J16.6, R1.1, R3.2, R47.1, R48.1, R49.1, U1.16 (VSS), U1.31 (VSSA), U1.38 (VSS), U1.51 (VSS), U1.61 (VSS), U1.83 (VSS), U1.94 (VSS), U1.107 (VSS), U1.120 (VSS), U1.130 (VSS), U2.2 (GND), U5.4 (GND), U6.4 (GND), U7.4 (GND), U8.4 (GND), U9.4 (GND), U10.4 (GND), U11.4 (GND), U12.4 (GND), X1.2 (GND), X2.2 (GND); also elsewhere on the board
unnamed: C18.1, U1.71 (VCAP1)
unnamed: C19.1, U1.106 (VCAP2)
unnamed: C58.1, J2.1
unnamed: FB1.1, J2.5, U2.5 (VBUS)
unnamed: FB2.2, J6.2
unnamed: FB6.2, J11.2
unnamed: FB7.2, J12.2
unnamed: FB8.2, J13.2
unnamed: J1.2, R1.2, U1.138 (BOOT0)
unnamed: J5.1, R44.1
unnamed: J5.2, R47.2
unnamed: J5.3, R45.1
unnamed: J5.4, R48.2
unnamed: J5.5, R46.1
unnamed: J5.6, R49.2
PWR1: J7.3, J7.5; also elsewhere on the board
PWR2: J7.11, J7.13; also elsewhere on the board
PWR3: J8.3, J8.5; also elsewhere on the board
PWR4: J8.11, J8.13; also elsewhere on the board
PWR5: J9.3, J9.5; also elsewhere on the board
PWR6: J9.11, J9.13; also elsewhere on the board
PWR7: J10.3, J10.5; also elsewhere on the board
PWR8: J10.11, J10.13; also elsewhere on the board

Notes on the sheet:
C17 is currently close enough to DC this. And at 32.768kHz... eh not worried.

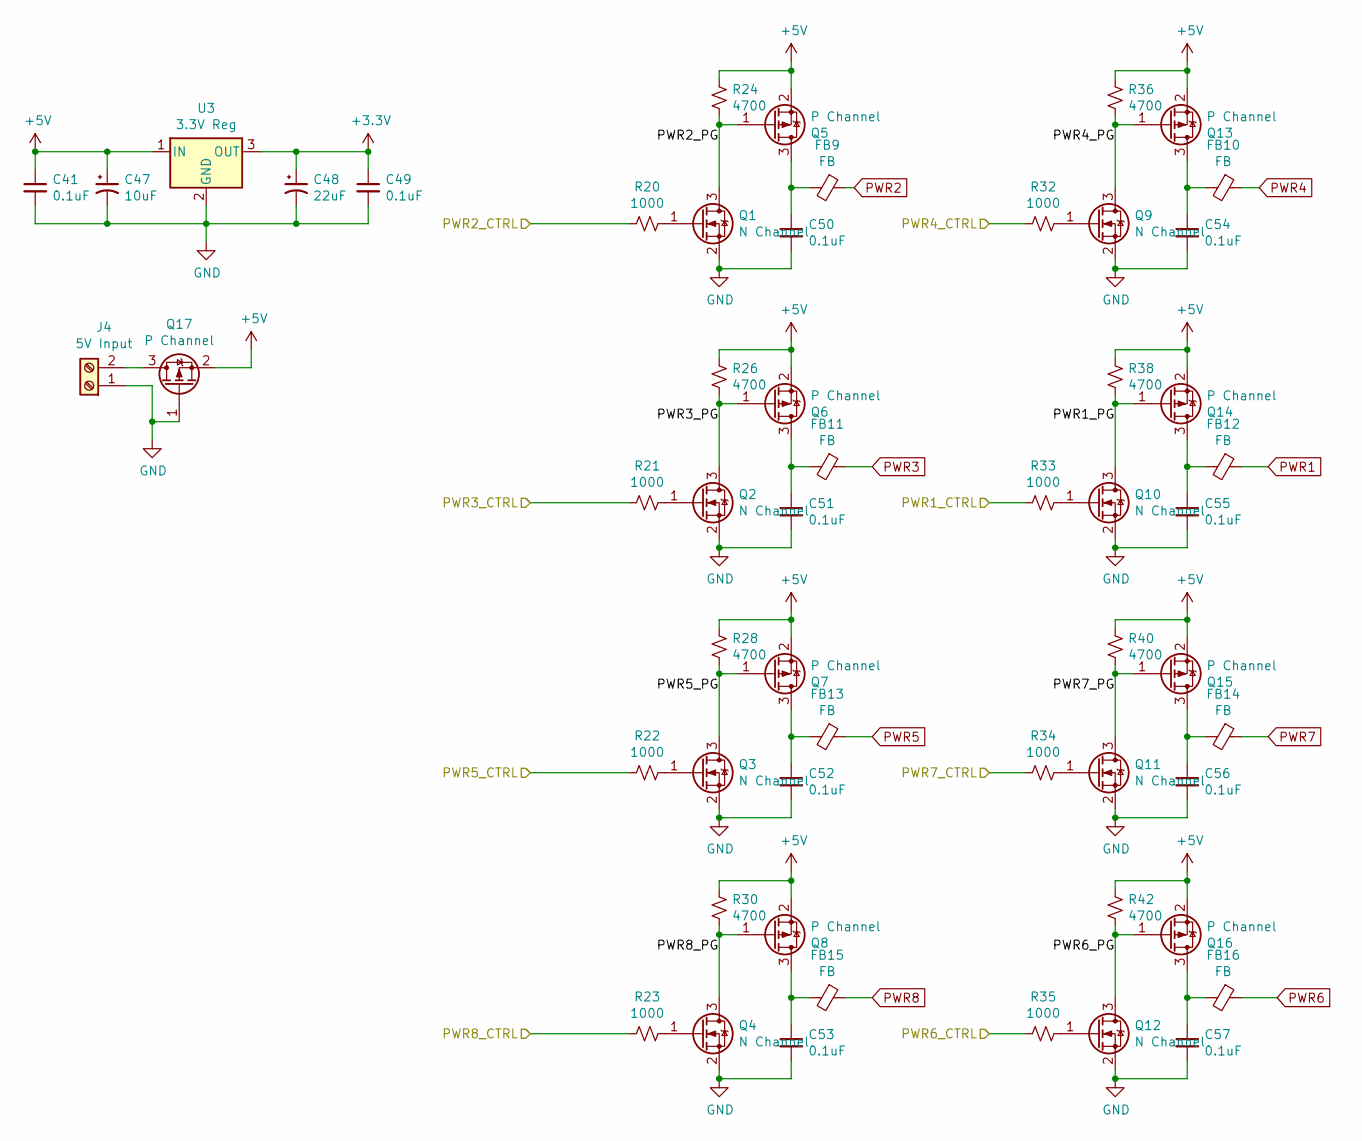
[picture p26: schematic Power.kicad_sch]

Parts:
C41, C49, C50, C51, C52, C53, C54, C55, C56, C57: 0.1uF; C_0805_2012Metric
C47: 10uF; CP_Elec_5x5.3
C48: 22uF; CP_Elec_6.3x5.8
FB9, FB10, FB11, FB12, FB13, FB14, FB15, FB16: FB; L_0805_2012Metric_Pad1.05x1.20mm_HandSolder
J4: 5V Input; TerminalBlock_bornier-2_P5.08mm
Q1, Q2, Q3, Q4, Q9, Q10, Q11, Q12: N Channel; SOT-23
Q5, Q6, Q7, Q8, Q13, Q14, Q15, Q16, Q17: P Channel; SOT-23
R20, R21, R22, R23, R32, R33, R34, R35: 1000; R_0805
R24, R26, R28, R30, R36, R38, R40, R42: 4700; R_0805
U3: 3.3V Reg; TO-220-3_Vertical

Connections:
+5V: C41.1, C47.1, Q5.2 (S), Q6.2 (S), Q7.2 (S), Q8.2 (S), Q13.2 (S), Q14.2 (S), Q15.2 (S), Q16.2 (S), Q17.2 (S), R24.1, R26.1, R28.1, R30.1, R36.1, R38.1, R40.1, R42.1, U3.1 (IN)
/PWR1_CTRL: R33.2; also elsewhere on the board
/PWR2_CTRL: R20.2; also elsewhere on the board
/PWR3_CTRL: R21.2; also elsewhere on the board
/PWR4_CTRL: R32.2; also elsewhere on the board
/PWR5_CTRL: R22.2; also elsewhere on the board
/PWR6_CTRL: R35.2; also elsewhere on the board
/PWR7_CTRL: R34.2; also elsewhere on the board
/PWR8_CTRL: R23.2; also elsewhere on the board
/Power/PWR1_PG: Q10.3 (D), Q14.1 (G), R38.2
/Power/PWR2_PG: Q1.3 (D), Q5.1 (G), R24.2
/Power/PWR3_PG: Q2.3 (D), Q6.1 (G), R26.2
/Power/PWR4_PG: Q9.3 (D), Q13.1 (G), R36.2
/Power/PWR5_PG: Q3.3 (D), Q7.1 (G), R28.2
/Power/PWR6_PG: Q12.3 (D), Q16.1 (G), R42.2
/Power/PWR7_PG: Q11.3 (D), Q15.1 (G), R40.2
/Power/PWR8_PG: Q4.3 (D), Q8.1 (G), R30.2
GND: C41.2, C47.2, C48.2, C49.2, C50.2, C51.2, C52.2, C53.2, C54.2, C55.2, C56.2, C57.2, J4.1, Q1.2 (S), Q2.2 (S), Q3.2 (S), Q4.2 (S), Q9.2 (S), Q10.2 (S), Q11.2 (S), Q12.2 (S), Q17.1 (G), U3.2 (GND); also elsewhere on the board
unnamed: C50.1, FB9.2, Q5.3 (D)
unnamed: C51.1, FB11.2, Q6.3 (D)
unnamed: C52.1, FB13.2, Q7.3 (D)
unnamed: C53.1, FB15.2, Q8.3 (D)
unnamed: C54.1, FB10.2, Q13.3 (D)
unnamed: C55.1, FB12.2, Q14.3 (D)
unnamed: C56.1, FB14.2, Q15.3 (D)
unnamed: C57.1, FB16.2, Q16.3 (D)
unnamed: J4.2, Q17.3 (D)
unnamed: Q1.1 (G), R20.1
unnamed: Q2.1 (G), R21.1
unnamed: Q3.1 (G), R22.1
unnamed: Q4.1 (G), R23.1
unnamed: Q9.1 (G), R32.1
unnamed: Q10.1 (G), R33.1
unnamed: Q11.1 (G), R34.1
unnamed: Q12.1 (G), R35.1
PWR1: FB12.1; also elsewhere on the board
PWR2: FB9.1; also elsewhere on the board
PWR3: FB11.1; also elsewhere on the board
PWR4: FB10.1; also elsewhere on the board
PWR5: FB13.1; also elsewhere on the board
PWR6: FB16.1; also elsewhere on the board
PWR7: FB14.1; also elsewhere on the board
PWR8: FB15.1; also elsewhere on the board

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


Board: 4 copper layers, 100.0 x 100.0 mm, 152 parts (3 on the bottom side), 139 nets.

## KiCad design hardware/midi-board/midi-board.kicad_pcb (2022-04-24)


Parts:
C2: 4.7uF; C_0805_2012Metric_Pad1.18x1.45mm_HandSolder
C3, C4, C6, C7, C8: 0.1uF; C_0805_2012Metric_Pad1.18x1.45mm_HandSolder
D1: Vf>=4; D_SOD-123F
FB1, FB2, FB3, FB4: Ferrite; L_0805_2012Metric_Pad1.05x1.20mm_HandSolder
FB5, FB6: FB; L_0805_2012Metric_Pad1.05x1.20mm_HandSolder
H1, H2, H3: MountingHole; MountingHole_3.2mm_M3
J1: MIDI OUT; SDS-50J
J2: MIDI IN; SDS-50J
J3, J6: Qwiic; JST_SH_SM04B-SRSS-TB_04x1.00mm_Angled
J4: Serial Wire; PinHeader_1x05_P2.54mm_Vertical
J7: UART; Pin_Header_Straight_1x03_Pitch2.54mm
J8: I2C; Pin_Header_Straight_1x04_Pitch2.54mm
J10: Conn_02x02_Odd_Even; Pin_Header_Straight_2x02_Pitch2.54mm
Q1, Q2: Q_NPN_BEC; SOT-23
R1: R_A; R_0805_2012Metric_Pad1.20x1.40mm_HandSolder
R2: R_O; R_0805_2012Metric_Pad1.20x1.40mm_HandSolder
R3: R_C; R_0805_2012Metric_Pad1.20x1.40mm_HandSolder
R4: 220; R_0805_2012Metric_Pad1.20x1.40mm_HandSolder
R5, R6: 10k; R_0805_2012Metric_Pad1.20x1.40mm_HandSolder
TP1, TP2, TP3: TestPoint; TestPoint_Pad_D1.0mm
U1: STM32G030Fx; TSSOP-20_4.4x6.5mm_P0.65mm
U3: TLP185(SE; SO-6_4.4x3.6mm_Pitch1.27mm

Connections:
/IRQ: R6.2, U1.15 (PB0/PB1/PB2/PA8)
/NRST: J4.2, U1.6 (NRST)
/RX: J7.2, R2.2, U1.10 (PA3), U3.6
/SCL: J3.4, J6.4, J8.4, U1.16 (PA11[PA9])
/SDA: J3.3, J6.3, J8.3, U1.17 (PA12[PA10])
/SWCLK: J4.3, U1.19 (PA15/PA14-BOOT0)
/SWDIO: J4.4, U1.18 (PA13)
/~TX: J7.3, R5.1, U1.9 (PA2)
GND: C2.1, C3.1, C4.1, C6.1, C7.1, C8.1, J1.2, J1.6 (Shield), J3.1, J4.5, J6.1, J7.1, J8.1, J10.2, J10.4, Q1.2 (E), Q2.2 (E), U1.5 (VSS/VSSA), U3.4
unnamed: C3.2, J2.2
unnamed: C4.2, J2.6 (Shield)
unnamed: D1.1 (K), R4.1, U3.1
unnamed: D1.2 (A), FB4.1, U3.3
unnamed: FB1.1, J1.4
unnamed: FB1.2, R1.2
unnamed: FB2.1, R3.2
unnamed: FB2.2, J1.5
unnamed: FB3.1, J2.4
unnamed: FB3.2, R4.2
unnamed: FB4.2, J2.5
unnamed: FB5.1, J3.2
unnamed: FB6.1, J6.2
unnamed: J10.1, J10.3, Q2.3 (C)
unnamed: Q1.1 (B), R5.2
unnamed: Q1.3 (C), R3.1
unnamed: Q2.1 (B), R6.1
unnamed: TP1.1, U1.2 (PB9/PC14-OSC32_IN)
unnamed: TP2.1, U1.1 (PB7/PB8)
unnamed: TP3.1, U1.20 (PB3/PB4/PB5/PB6)

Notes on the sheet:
MIDI specs talk about the ferrite bead specs, but we're not really sensitive to them. The signal is extremely low frequency, so the more the beads cut out the better. I don't think you could possibly use beads that are "too strong".
When IRQ goes high, we pull the line to ground. The main board will pull the IRQ lines weakly high. And we're specifying a BJT here, since we're already using a BJT elsewhere.
R_0 should be >=330Ω
Per MIDI spec, none of the input connections go straight to ground. Instead they're run through small ceramic caps.
Note, we rely on the STM32 to invert its TX signal into ~{TX}, so that we can drive an N-channel FET directly.
You can probably swap the TLP185 for most anything that fits and has the matching pinout. R_O might need to be tweaked, depending on the exact phototransistor attributes.
Thought about using a MOSFET here, to reduce BOM, but: 1) Properly limiting the sink/source current from the uC pin might mean that we can't switch the MOSFET at MIDI data rates, without paying careful attention to MOSFET specs. Which I'd prefer to avoid. 2) On MOSFET will be a dead-short, which is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
Serial Wire Debug header. There's no standard pinout I'm aware of, so this is what I'm using on this project's boards.
D1 is RP protection for the optoisolator. Technically optional. If you're going to install it, pick one with a Vf less than the reverse breakdown of the optoisolator, which will be ~5V.
Dramatically limit current into the base. We only need to let a tiny bit of current through for the optoisolator on the other end to trigger.
You could duplicate the DIN connectors and associated circuitry, and use both UARTs.

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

Board: 2 copper layers, 88.0 x 45.8 mm, 37 parts (0 on the bottom side), 30 nets.

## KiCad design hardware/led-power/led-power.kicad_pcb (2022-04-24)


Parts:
C1, C2, C3, C4, C5, C6, C7, C8, C10, C11, C12, C13, C14, C15, C16, C17, C18, C20, C30: .1uF; C_0805_2012Metric_Pad1.18x1.45mm_HandSolder
C9: Lots; CP_Radial_D16.0mm_P7.50mm
C21: 4.7uF; C_0805_2012Metric_Pad1.18x1.45mm_HandSolder
C22: 0.1uF; C_0805_2012Metric_Pad1.18x1.45mm_HandSolder
C23: 300pF; C_0805_2012Metric_Pad1.18x1.45mm_HandSolder
C29: 2.2uF; C_0805_2012Metric_Pad1.18x1.45mm_HandSolder
D1, D2, D3, D4, D5, D6, D7, D8: LED; LED_0805_2012Metric_Pad1.15x1.40mm_HandSolder
D9: D_Small_ALT; D_SOD-123F
D10: 2.2Vf; LED_0805_2012Metric_Pad1.15x1.40mm_HandSolder
H1, H2, H3, H4: MountingHole_Pad; MountingHole_3.2mm_M3
J1: String1; Pin_Header_Angled_1x02_Pitch2.54mm
J2: String2; Pin_Header_Angled_1x02_Pitch2.54mm
J3: String3; Pin_Header_Angled_1x02_Pitch2.54mm
J4: String4; Pin_Header_Angled_1x02_Pitch2.54mm
J5: String5; Pin_Header_Angled_1x02_Pitch2.54mm
J6: String6; Pin_Header_Angled_1x02_Pitch2.54mm
J7: String7; Pin_Header_Angled_1x02_Pitch2.54mm
J8: String8; Pin_Header_Angled_1x02_Pitch2.54mm
J9: PowerInput; TerminalBlock_bornier-2_P5.08mm
J10: Conn_01x05_Male; PinHeader_1x05_P2.54mm_Vertical
J11, J12: Qwiic; JST_SH_SM04B-SRSS-TB_04x1.00mm_Angled
J16: I2C Header; Pin_Header_Straight_1x04_Pitch2.54mm
J17: IRQ; Pin_Header_Straight_1x02_Pitch2.54mm
Q1, Q2, Q3, Q4, Q5, Q6, Q7, Q8: Q_NMOS_GDS; TO-220-3_Vertical
Q9: Q_NPN_BEC; SOT-23
R1, R2, R3, R4, R5, R6, R7, R8: 100; R_Axial_DIN0207_L6.3mm_D2.5mm_P2.54mm_Vertical
R9: 3600; R_0805_2012Metric_Pad1.20x1.40mm_HandSolder
R10: 10k; R_0805_2012Metric_Pad1.20x1.40mm_HandSolder
R11: 1000; R_0805_2012Metric_Pad1.20x1.40mm_HandSolder
R12: 6800; R_0805_2012Metric_Pad1.20x1.40mm_HandSolder
R24: 2400; R_0805_2012Metric_Pad1.20x1.40mm_HandSolder
R25: 110k; R_0805_2012Metric_Pad1.20x1.40mm_HandSolder
R27: 4.7k; R_0805_2012Metric_Pad1.20x1.40mm_HandSolder
U1, U2, U3, U4, U5, U6, U7, U8: MCP6V51; MSOP-8_3x3mm_Pitch0.65mm
U9: STM32G030Fx; TSSOP-20_4.4x6.5mm_P0.65mm
U10: L78L05ACZ-AP; TO-92_Inline_Wide
U11: MCP1501; SOIC-8-N
U12: LM317_TO-220; TO-220-3_Vertical

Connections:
+3V3: C21.1, C22.1, J10.1, J11.2, J12.2, J16.2, U9.4 (VDD/VDDA)
+5V: C20.1, C29.1, R9.1, U10.1 (VOUT), U11.1 (VDD)
+12V: C11.1, C12.1, C13.1, C14.1, C15.1, C16.1, C17.1, C18.1, C30.1, R11.1, U1.7 (V+), U2.7 (V+), U3.7 (V+), U4.7 (V+), U5.7 (V+), U6.7 (V+), U7.7 (V+), U8.7 (V+), U10.3 (VIN), U12.2 (VO)
+48V: C9.1, C10.1, D1.2 (A), D2.2 (A), D3.2 (A), D4.2 (A), D5.2 (A), D6.2 (A), D7.2 (A), D8.2 (A), D9.1 (K), R25.1, U12.3 (VI)
/48V_SENSE: R25.2, R27.1, U9.8 (PA1)
/Feedback1: Q1.3 (S), R1.1, U1.2 (-), U9.12 (PA5)
/Feedback2: Q2.3 (S), R2.1, U2.2 (-), U9.11 (PA4)
/Feedback3: Q3.3 (S), R3.1, U3.2 (-), U9.9 (PA2)
/Feedback4: Q4.3 (S), R4.1, U4.2 (-), U9.10 (PA3)
/Feedback5: Q5.3 (S), R5.1, U5.2 (-), U9.1 (PB7/PB8)
/Feedback6: Q6.3 (S), R6.1, U6.2 (-), U9.15 (PB0/PB1/PB2/PA8)
/Feedback7: Q7.3 (S), R7.1, U7.2 (-), U9.14 (PA7)
/Feedback8: Q8.3 (S), R8.1, U8.2 (-), U9.13 (PA6)
/IRQ: R10.2, U9.2 (PB9/PC14-OSC32_IN)
/NRST: J10.2, U9.6 (NRST)
/SCL: J11.4, J12.4, J16.4, U9.16 (PA11[PA9])
/SDA: J11.3, J12.3, J16.3, U9.17 (PA12[PA10])
/SWCLK: J10.3, U9.19 (PA15/PA14-BOOT0)
/SWDIO: J10.4, U9.18 (PA13)
/VREF: C23.1, R24.2, U1.3 (+), U2.3 (+), U3.3 (+), U4.3 (+), U5.3 (+), U6.3 (+), U7.3 (+), U8.3 (+), U11.7 (OUT), U11.8 (FEEDBACK)
/~SHDN: R9.2, U9.20 (PB3/PB4/PB5/PB6), U11.3 (/SHDN)
GND: C1.2, C2.2, C3.2, C4.2, C5.2, C6.2, C7.2, C8.2, C9.2, C10.2, C11.2, C12.2, C13.2, C14.2, C15.2, C16.2, C17.2, C18.2, C20.2, C21.2, C22.2, C23.2, C29.2, C30.2, D10.1 (K), J9.2, J10.5, J11.1, J12.1, J16.1, J17.2, Q9.2 (E), R1.2, R2.2, R3.2, R4.2, R5.2, R6.2, R7.2, R8.2, R24.1, R27.2, U1.4 (V-), U2.4 (V-), U3.4 (V-), U4.4 (V-), U5.4 (V-), U6.4 (V-), U7.4 (V-), U8.4 (V-), U9.5 (VSS/VSSA), U10.2 (GND), U11.2 (GND), U11.4 (GND), U11.5 (GND), U11.6 (GND)
unnamed: C1.1, D1.1 (K), J1.1
unnamed: C2.1, D2.1 (K), J2.1
unnamed: C3.1, D3.1 (K), J3.1
unnamed: C4.1, D4.1 (K), J4.1
unnamed: C5.1, D5.1 (K), J5.1
unnamed: C6.1, D6.1 (K), J6.1
unnamed: C7.1, D7.1 (K), J7.1
unnamed: C8.1, D8.1 (K), J8.1
unnamed: D9.2 (A), J9.1
unnamed: D10.2 (A), R12.2
unnamed: J1.2, Q1.2 (D)
unnamed: J2.2, Q2.2 (D)
unnamed: J3.2, Q3.2 (D)
unnamed: J4.2, Q4.2 (D)
unnamed: J5.2, Q5.2 (D)
unnamed: J6.2, Q6.2 (D)
unnamed: J7.2, Q7.2 (D)
unnamed: J8.2, Q8.2 (D)
unnamed: J17.1, Q9.3 (C)
unnamed: Q1.1 (G), U1.6
unnamed: Q2.1 (G), U2.6
unnamed: Q3.1 (G), U3.6
unnamed: Q4.1 (G), U4.6
unnamed: Q5.1 (G), U5.6
unnamed: Q6.1 (G), U6.6
unnamed: Q7.1 (G), U7.6
unnamed: Q8.1 (G), U8.6
unnamed: Q9.1 (B), R10.1
unnamed: R11.2, R12.1, U12.1 (ADJ)

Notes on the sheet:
Meanwell HDR-30-48 (adjust DOWN, reduces heat in FETs)
This will be just under 12V at full load. We probably won't hit full load, so it will rise slightly, giving us a bit more than 12V. Should see about 1.25mA through the LED. Raising the 6.8K will increase the voltage. If your MOSFETs need _extremely_ high gate voltages, you _might_ need to do that.
To drain the VREF net when /SHDN is active.


Board: 4 copper layers, 86.4 x 86.4 mm, 88 parts (0 on the bottom side), 51 nets.

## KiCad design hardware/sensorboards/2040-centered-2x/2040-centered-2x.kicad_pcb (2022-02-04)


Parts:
H1, H2: MountingHole; MountingHole_3.2mm_M3
J1: Conn_01x06_Male; Pin_Header_Angled_1x06_Pitch2.54mm
TP1: TestPoint; TestPoint_Pad_1.0x1.0mm
U1, U2: CNY70; Vishay_CNY70

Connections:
/NEG: J1.1, U2.2 (K)
/POS: J1.6, U1.1 (A)
unnamed: J1.2, U2.4 (E)
unnamed: J1.3, U2.3 (C)
unnamed: J1.4, U1.4 (E)
unnamed: J1.5, U1.3 (C)
unnamed: TP1.1, U1.2 (K), U2.1 (A)


Board: 2 copper layers, 20.5 x 48.0 mm, 6 parts (1 on the bottom side), 7 nets.

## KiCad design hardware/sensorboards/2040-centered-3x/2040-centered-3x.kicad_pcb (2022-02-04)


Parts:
H1, H2, H3, H4: MountingHole; MountingHole_3.2mm_M3
J1: Conn_01x08_Male; PinHeader_1x08_P2.54mm_Horizontal
TP1, TP2: TestPoint; TestPoint_Pad_1.0x1.0mm
U1, U2, U3: CNY70; Vishay_CNY70

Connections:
/C1: J1.7, U1.3 (C)
/C2: J1.5, U2.3 (C)
/C3: J1.3, U3.3 (C)
/E1: J1.6, U1.4 (E)
/E2: J1.4, U2.4 (E)
/E3: J1.2, U3.4 (E)
/NEG: J1.1, U3.2 (K)
/POS: J1.8, U1.1 (A)
unnamed: TP1.1, U1.2 (K), U2.1 (A)
unnamed: TP2.1, U2.2 (K), U3.1 (A)


Board: 2 copper layers, 33.2 x 48.1 mm, 10 parts (1 on the bottom side), 10 nets.

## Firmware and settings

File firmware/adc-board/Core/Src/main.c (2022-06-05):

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
/* Includes ------------------------------------------------------------------*/
#include "main.h"
#include "usb_device.h"

/* USER CODE BEGIN Includes */
//#include "usbd_cdc_if.h"
#include "hdlc.h"
/* USER CODE END Includes */

ADC_HandleTypeDef hadc1;
ADC_HandleTypeDef hadc2;
ADC_HandleTypeDef hadc3;
DMA_HandleTypeDef hdma_adc1;
DMA_HandleTypeDef hdma_adc2;
DMA_HandleTypeDef hdma_adc3;

TIM_HandleTypeDef htim1;

UART_HandleTypeDef huart1;
UART_HandleTypeDef huart2;
UART_HandleTypeDef huart3;
DMA_HandleTypeDef hdma_usart3_rx;
DMA_HandleTypeDef hdma_usart3_tx;

void SystemClock_Config(void);
void PeriphCommonClock_Config(void);
static void MX_GPIO_Init(void);
static void MX_DMA_Init(void);
static void MX_ADC1_Init(void);
static void MX_ADC2_Init(void);
static void MX_ADC3_Init(void);
static void MX_USART1_UART_Init(void);
static void MX_USART3_UART_Init(void);
static void MX_USART2_UART_Init(void);
static void MX_TIM1_Init(void);
/* USER CODE BEGIN 0 */

// important stuff in here!
struct systemstatus status;

// we should compute sample_rate from the clock
// and timer configuration.
uint32_t sample_rate = 20000;

// Our DMA buffer is DMASIZE samples deep, and we don't get an interrupt
// until it is full. So when it is >1, we only run our DSP every that many
// samples. No samples are dropped! We just don't process every time.
#define DMASIZE 2

// Instruct the compiler to align these to cache-line boundaries
// They'll always be read/written as blocks, independently from
// the others, or anything else.
// We also move them into the .dmabuffers section, which is the
// only thing in RAM_D3, so as to minimize contention between
// DMA copying the ADC values into RAM, and everything else we do.
__attribute__ ((aligned (32))) __attribute__(( section(".dmabuffers") )) uint16_t adc1_buffer[7*DMASIZE];
// adc2 drops some DMAs here and there.
__attribute__ ((aligned (32))) __attribute__(( section(".dmabuffers") )) uint16_t adc2_buffer[7*DMASIZE];
__attribute__ ((aligned (32))) __attribute__(( section(".dmabuffers") )) uint16_t adc3_buffer[8*DMASIZE];

// Represents what we need to know for a sensor.
// Values in here should only be altered by external
// configuration processes.
// updates to this structure should be done as atomically
// as possible. prepare a new copy on the stack, disable
// interrupts, bcopy into this array, and reenable.
// TODO get this stored in DTCM
struct sensorconf {
	// True means we're watching a hammer; rises only
	_Bool hammer;
	// Hammer stuff
	// absolute position must be above this to trigger derivative calculations
	// that's a prereq for a note to occur. it should, ideally, be between
	// "impact" and the let off point.
	float minpos;

	// Key stick stuff
	int hammerchan; // corresponding hammer
	float offpos;     // reading at which to trip to off
} conf[22];

struct sensorstate {
	uint32_t notesent; // 0=nothing sent recently, otherwise time of send
	float sentval; // the velocity we sent.
	_Bool damperup;
	_Bool notesounding; // we've sent a noteon, and haven't yet sent a noteoff for it
} state[22];

uint16_t collectstats = 0;
struct sensorstat {
	uint16_t min;
	uint16_t max;
	uint32_t sum;
	uint32_t count;
} stats[22];

struct __attribute__((__packed__)) sensortrip {
	float velocity;
	uint8_t chan;
};

#define BUFSIZE 32
// TODO move these into DTCM
int bufferptrs[3] = { 0 }; // points to the locations we'll write to next. one past the most recent value.
float sensorbuffer[22][BUFSIZE] = { 0.0 };
float derivs[22][3] = { 0.0 } ;
int derividxs[22] = { 0 };

#define FIR_LEN 13
// TODO want this in DTCM also
// scipy.signal.savgol_coeffs(13, 2, deriv=1, use='dot', delta=0.01)
// the delta doesn't matter, so it was chosen to bring the values to ~1.0
float filter[FIR_LEN] = { -3.2967032967033107, -2.7472527472527473,
		-2.197802197802188, -1.64835164835163, -1.0989010989010746,
		-0.5494505494505213, 2.9531932455029164e-14, 0.5494505494505779,
		1.098901098901124, 1.6483516483516676, 2.1978021978022086,
		2.7472527472527473, 3.296703296703284 };
// supposedly argerich can play 11.52 notes/second
// 16000 samples per second. let's leave her some room,
// and assume 16 notes/second. 16000/16 = 1000
#define MINCYCLESBETWEENNOTES 500

_Bool update_setting(uint8_t channel, uint8_t setting, uint32_t value)
{
	if(channel<0 || channel>=22) {
		return 0;
	}
	switch(setting) {
	case 0: {
		// channel type
		if(value==0 || value==1) {
			conf[channel].hammer = value;
			return 1;
		}
		break;
	}
	case 1: {
		// hammer minpos
		float v = *((float *)&value);
		if(conf[channel].hammer && v>1.0 && v<65535.0) {
			conf[channel].minpos = v;
			return 1;
		}
		break;
	}
	case 2: {
		// damper off pos
		float v = *((float *)&value);
		if((!conf[channel].hammer) && v>1.0 && v<65535.0) {
			conf[channel].offpos = v;
			return 1;
		}
		break;
	}
	case 3: {
		// hammer channel for this dampener
		if(conf[channel].hammer)
			// channel is a hammer, not a dampener, can't set this.
			return 0;
		if(value<0 || value>=22)
			// channel out of range
			return 0;
		if(!conf[value].hammer)
			// target channel isn't a hammer!
			return 0;
		conf[channel].hammerchan = value;
		return 1;
	}
	}

	// couldn't successfully process whatever it was.
	return 0;
}

/* USER CODE END 0 */

/**
  * @brief  The application entry point.
  * @retval int
  */
int main(void)
{
  /* Enable I-Cache---------------------------------------------------------*/
  SCB_EnableICache();

  /* MCU Configuration--------------------------------------------------------*/

  /* Reset of all peripherals, Initializes the Flash interface and the Systick. */
  HAL_Init();

  /* Configure the system clock */
  SystemClock_Config();

/* Configure the peripherals common clocks */
  PeriphCommonClock_Config();

  /* Initialize all configured peripherals */
  MX_GPIO_Init();
  MX_DMA_Init();
  MX_ADC1_Init();
  MX_ADC2_Init();
  MX_ADC3_Init();
  MX_USART1_UART_Init();
  MX_USART3_UART_Init();
  MX_USART2_UART_Init();
  MX_USB_DEVICE_Init();
  MX_TIM1_Init();
  /* USER CODE BEGIN 2 */

  HDLC_Init(&huart3, &hdma_usart3_rx);

  // put some plausible values in the autodetection routines.
  // and get the state initialized.
  for(int i=0; i<22; i++) {
	  // hammer default
	  conf[i].minpos = 15000;

	  // keystick default
	  conf[i].offpos = 9000;

	  state[i].notesent = 0;
	  state[i].sentval = 0.0;
	  state[i].damperup = 0;
	  state[i].notesounding = 0;
  }
  // the hammers
  conf[0].hammer = 1;
  conf[1].hammer = 1;
  conf[2].hammer = 1;
  conf[4].hammer = 1;
  conf[6].hammer = 1;
  conf[9].minpos = 20000;
  conf[9].hammer = 1;
  conf[10].hammer = 1;
  conf[18].hammer = 1;
  conf[18].minpos = 12000;
  conf[19].hammer = 1;
  conf[20].hammer = 1;
  conf[21].hammer = 1;
  // key sticks
  conf[3].hammerchan = 2;
  conf[5].hammerchan = 6;
  conf[5].offpos = 5000;
  conf[7].hammerchan = 0;
  conf[7].offpos = 5000;
  conf[8].hammerchan = 10;
  conf[11].hammerchan = 9;
  conf[11].offpos = 5000;
  conf[12].hammerchan = 1;
  conf[13].hammerchan = 4;
  conf[13].offpos = 5000;
  conf[14].hammerchan = 18;
  conf[15].hammerchan = 19;
  conf[16].hammerchan = 20;
  conf[17].hammerchan = 21;

  HAL_Delay(10);
  HAL_ADCEx_Calibration_Start(&hadc1, ADC_CALIB_OFFSET, ADC_SINGLE_ENDED);
  HAL_Delay(10);
  HAL_ADCEx_Calibration_Start(&hadc2, ADC_CALIB_OFFSET, ADC_SINGLE_ENDED);
  HAL_Delay(10);
  HAL_ADCEx_Calibration_Start(&hadc3, ADC_CALIB_OFFSET, ADC_SINGLE_ENDED);
  HAL_Delay(10);


  {
	  // fill out / initialize the system status struct
	  status.uniqueid[0] = HAL_GetUIDw0();
	  status.uniqueid[1] = HAL_GetUIDw1();
	  status.uniqueid[2] = HAL_GetUIDw2();
	  status.devid = HAL_GetDEVID();
	  status.revid = HAL_GetREVID();
	  // derived this expression from the code for HAL_GetUIDw0
	  status.flashsize = READ_REG(*((uint32_t *)FLASHSIZE_BASE));

	  // this one is actually important, we use it in places
	  status.sample_time = 0;
	  status.adc1_dmas = 0;
	  status.adc2_dmas = 0;
	  status.adc3_dmas = 0;
  }

  HDLC_Send_Frame(&huart3, 0x03, "calibdone", 9);
  HDLC_Send_Frame(&huart3, 0x03, "calibdone", 9);
  HDLC_Send_Frame(&huart3, 0x03, "calibdone", 9);

  HAL_TIM_Base_Start_IT(&htim1);

  // start timer
  HAL_ADC_Start_DMA(&hadc1, (uint32_t*)adc1_buffer, 7*DMASIZE);
  HAL_ADC_Start_DMA(&hadc2, (uint32_t*)adc2_buffer, 7*DMASIZE);
  HAL_ADC_Start_DMA(&hadc3, (uint32_t*)adc3_buffer, 8*DMASIZE);
  HAL_TIM_PWM_Start(&htim1, TIM_CHANNEL_1);
  HAL_TIM_PWM_Start(&htim1, TIM_CHANNEL_2);
  HAL_TIM_PWM_Start(&htim1, TIM_CHANNEL_3);
  HAL_TIM_OC_Start(&htim1, TIM_CHANNEL_4);

  /* USER CODE END 2 */

  /* Infinite loop */
  /* USER CODE BEGIN WHILE */

  uint32_t last_clock_pulse = 1<<30;
  while (1)
  {
	  // we'll wake up occasionally.
	  __asm("wfi");

	  // how much time has passed since our last clock message?
	  // if(lots) { output new clock message }
	  uint32_t clock_rate = sample_rate * 64; // 64 seconds; should be a bitshift
	  if(  ((status.sample_time < last_clock_pulse) &&
		    ((UINT32_MAX - last_clock_pulse) + status.sample_time >= clock_rate))
		|| ((status.sample_time > last_clock_pulse) &&
			(status.sample_time - last_clock_pulse >= clock_rate)) ) {
		  // we've passed clock_rate worth of samples, so we'll send another clock message
		  HDLC_Send_Frame(&huart3, 0x07, (uint8_t*)&(status.sample_time), sizeof(uint32_t));
		  last_clock_pulse = status.sample_time;
	  }

	  if(collectstats) {
		  if((status.sample_time % collectstats)==0) {
			  // we should be collecting stats. send them out.
			  HDLC_Send_Frame(&huart3, 0x0C, (uint8_t*)stats, sizeof(stats));
			  for(int i=0; i<22; i++) {
				  stats[i].min = -1;
				  stats[i].max = 0;
				  stats[i].sum = 0;
				  stats[i].count = 0;
			  }
		  }
	  }

    /* USER CODE END WHILE */

    /* USER CODE BEGIN 3 */
  }
  /* USER CODE END 3 */
}

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
/* USER CODE BEGIN 4 */

void HAL_TIM_PeriodElapsedCallback(TIM_HandleTypeDef *htim)
{
	if(htim == &htim1) {
		status.sample_time += 1;
	}
}

void HAL_UART_TxCpltCallback(UART_HandleTypeDef *huart)
{
	if(huart==&huart3)
		HDLC_DMA_Send_Complete(huart);
}

static inline __attribute__((always_inline)) float computefilter(int chan, int idxs[])
{
	float v = 0.0;
	for(int i=0; i<FIR_LEN; i++) {
		// TODO check to see what the compiler-emitted assembly looks like.
		// if we're not using the fused multiply and add instruction, fix it.
		v += filter[i] * sensorbuffer[chan][idxs[i]];
	}
	return v;
}

static inline uint16_t min(uint16_t a, uint16_t b) {
	return (a<b) ? a : b;
}

static inline uint16_t max(uint16_t a, uint16_t b) {
	return (a>b) ? a : b;
}

// TODO move this into ITCM?
void HAL_ADC_ConvCpltCallback(ADC_HandleTypeDef *hadc)
{
	uint32_t now = status.sample_time;

	// Set up the variations on the copy loop
	uint16_t *buf;
	int cnt = 7;
	int offset = 0;
	int whichadc;
	int idxs[FIR_LEN] = {0};
	if(hadc==&hadc1) {
		buf = adc1_buffer;
		whichadc = 0;
		status.adc1_dmas++;
	} else if(hadc==&hadc2) {
		buf = adc2_buffer;
		offset = 7;
		whichadc = 1;
		status.adc2_dmas++;
	} else if(hadc==&hadc3){
		buf = adc3_buffer;
		cnt = 8;
		offset = 14;
		whichadc = 2;
		status.adc3_dmas++;
	} else {
		return;
	}

	int bufptr = bufferptrs[whichadc];

	uint16_t sendbuffer[DMASIZE];
	uint8_t TARGETCHANNEL = 100;

	// Copy the ADC buffers into the main circular buffer.
	for(int samp=0; samp<DMASIZE; samp++) {
		// each channel in there
		for(int i=0; i<cnt; i++) {
			int chan = offset+i;
			uint16_t v = 65535 - buf[samp*cnt+i];
			sensorbuffer[chan][(bufptr+samp) % BUFSIZE] = (float)(v);

			if(chan==TARGETCHANNEL) {
				sendbuffer[samp] = v;
			}

			if(collectstats) {
				stats[chan].min = min(stats[chan].min, v);
				stats[chan].max = max(stats[chan].max, v);
				stats[chan].count++;
				stats[chan].sum += v;
			}
		}
	}

	if(offset <= TARGETCHANNEL && TARGETCHANNEL < offset + cnt) {
		HDLC_Send_Frame(&huart3, 0x0A, (uint8_t*)sendbuffer, DMASIZE * sizeof(uint16_t));
	}

	// update bufferptrs to reflect new data
	bufptr = bufferptrs[whichadc] = (bufferptrs[whichadc] + DMASIZE) % BUFSIZE;

	// if we've been asked to stream a sensor out the serial port...
	if(0) {
		float buffer[1];
		buffer[0] = sensorbuffer[11][bufptr];
	    // read the DMASIZE values before bufptr
		HDLC_Send_Frame(&huart3, 0x0A, (uint8_t*)buffer, sizeof(buffer));
	}

	// TODO fill idxs with enough indexes to do two FIR/deriv calculations
	// for now-DMABUF/2 and now.
	for(int idx=0; idx<FIR_LEN; idx++) {
		// start from bufptr, which represents the next spot to write to
		// subtract one to get back to the most recent value
		// then go back by the length of the FIR filter
		// then add back the idx we want
		// that might be negative, so add BUFSIZE before doing %BUFSIZE.
		idxs[idx] = ((bufptr - 1 - FIR_LEN + idx) + BUFSIZE) % BUFSIZE;
	}
	// index of the middle value for the filter
	// division is right for odd numbers
	int mid = idxs[FIR_LEN/2];

#define INFDERIV(chan) { derivs[chan][derividxs[chan]] = INFINITY; derividxs[chan] = (1 + derividxs[chan]) % 3; }

	// We'll process the chunk we just got.
	for(int chan=offset; chan<offset+cnt; chan++) {
		if(conf[chan].hammer) {
			// Hammer

			// note that anywhere we skip this and don't compute the
			// derivative, we put +INF in for the current derivative.
			// this ensures that when we go to check to see if there
			// is a derivative peak, we don't use stale data.

			// This represents the "don't rapidly send multiple note-ons"
			// condition. At least MINCYCLESBETWEENNOTES has to pass before
			// we'll even look at the data again.
			if(state[chan].notesent) {
				// we've sent something recently.
				if(state[chan].notesent < now) {
					// no wrap situation
					if(state[chan].notesent < (now - MINCYCLESBETWEENNOTES)) {
						// enough time has passed.
						state[chan].notesent = 0;
					} else {
						// not enough time, ignore
						INFDERIV(chan);
						continue;
					}
				} else {
					// we've wrapped
					if((state[chan].notesent + MINCYCLESBETWEENNOTES) < now) {
						// also enough time as passed
						state[chan].notesent = 0;
					} else {
						// not enough time, ignore
						INFDERIV(chan);
						continue;
					}
				}
			}

			// This is the "the string can't sound until the hammer is close
			// enough" condition. If we're not close, don't look at the data.
			if(sensorbuffer[chan][mid] < conf[chan].minpos) {
				// hammer is too low
				INFDERIV(chan);
				continue;
			}

			// Ok, now we need the derivative
			float v = computefilter(chan, idxs);
			int didx = derividxs[chan]; // where we're putting our value
			derivs[chan][derividxs[chan]] = v;

			float derivold, derivmid, derivnew;
			derivnew = v;
			derivmid = derivs[chan][(didx + 3 - 1) % 3];
			derivold = derivs[chan][(didx + 3 - 2) % 3];

			// increment the spot we'll put the derivative
			derividxs[chan] = (1 + derividxs[chan]) % 3;

			// if derivmid is equal to either of the others, then we don't
			// actually trigger. but we're dealing with a float computed from
			// FIR_LEN input values. equality is unlikely.
			if(derivmid > 0.0 && derivmid > derivold && derivmid > derivnew) {
				state[chan].notesent = now;
				state[chan].sentval = v;
				state[chan].notesounding = 1;

				struct sensortrip msg;
				msg.chan = chan;
				msg.velocity = derivmid;
				HDLC_Send_Frame(&huart3, 0x08, (uint8_t*)&msg, sizeof(msg));
			}

		} else {
			// Key stick

			int hammerchan = conf[chan].hammerchan;

			// if the damper is up
			if(state[chan].damperup) {
				if(sensorbuffer[chan][mid] < conf[chan].offpos - 32) {
					// damper appears to have dropped back down.
					state[chan].damperup = 0;

					if(state[hammerchan].notesounding) {
						// our hammer has a note sounding. issue a note off.
						state[hammerchan].notesounding = 0;

						struct sensortrip msg;
						msg.chan = chan;
						// this is actually the derivative from a few
						// samples ago. good enough. key stick moves slowly.
						msg.velocity = computefilter(chan, idxs);
						HDLC_Send_Frame(&huart3, 0x08, (uint8_t*)&msg, sizeof(msg));
					}
				}
			} else {
				// damper is _down_
				if(sensorbuffer[chan][mid] > conf[chan].offpos + 32) {
					// damper appears to have been raised.
					state[chan].damperup = 1;

					// if we wanted to send "pre-lift" messages
					/*
					struct sensortrip msg;
					msg.chan = chan;
					msg.velocity = computefilter(chan, idxs);
					HDLC_Send_Frame(&huart3, 0x08, (uint8_t*)&msg, sizeof(msg));
					*/
				}
			}

/*
			if(state[hammerchan].notesounding) {
				if(sensorbuffer[chan][mid] < conf[chan].offpos) {
					// we've dropped low enough. we're dampening now,
					// so mark the note as stopped.
					state[hammerchan].notesounding = 0;
					state[hammerchan].damperup = 0;

					struct sensortrip msg;
					msg.chan = chan;
					// this is actually the derivative from a few
					// samples ago. good enough.
					msg.velocity = computefilter(chan, idxs);
					HDLC_Send_Frame(&huart3, 0x08, (uint8_t*)&msg, sizeof(msg));
				}
			}
*/
		}
	}
}

/* USER CODE END 4 */
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


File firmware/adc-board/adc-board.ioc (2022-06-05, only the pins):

Mcu.UserName=STM32H743ZGTx
PA0.GPIO_Label=Sen10
PA0.Signal=ADC1_INP16
PA1.GPIO_Label=Sen11
PA1.Signal=ADC1_INP17
PA10.GPIO_Label=TP27
PA10.Signal=GPIO_Input
PA11.Signal=USB_OTG_FS_DM
PA12.Signal=USB_OTG_FS_DP
PA2.GPIO_Label=Sen12
PA2.Signal=ADCx_INP14
PA3.GPIO_Label=Sen9
PA3.Signal=ADCx_INP15
PA4.GPIO_Label=Sen8
PA4.Signal=ADCx_INP18
PA5.GPIO_Label=Sen7
PA5.Signal=ADCx_INP19
PA6.GPIO_Label=Sen6
PA6.Signal=ADCx_INP3
PA7.GPIO_Label=Sen5
PA7.Signal=ADCx_INP7
PA8.GPIO_Label=TP26
PA8.Signal=GPIO_Input
PA9.Signal=USB_OTG_FS_VBUS
PB0.GPIO_Label=Sen2
PB0.Signal=ADCx_INP9
PB1.GPIO_Label=Sen1
PB1.Signal=ADCx_INP5
PB10.GPIO_Label=RS485_TX
PB10.Signal=USART3_TX
PB11.GPIO_Label=RS485_RX
PB11.Signal=USART3_RX
PB14.Signal=USART1_TX
PB15.Signal=USART1_RX
PC0.GPIO_Label=Sen14
PC0.Signal=ADCx_INP10
PC1.GPIO_Label=Sen13
PC1.Signal=ADCx_INP11
PC10.GPIO_Label=LED4
PC10.Signal=GPIO_Output
PC12.GPIO_Label=LED3
PC12.Signal=GPIO_Output
PC4.GPIO_Label=Sen4
PC4.Signal=ADCx_INP4
PC5.GPIO_Label=Sen3
PC5.Signal=ADCx_INP8
PC8.GPIO_Label=TP28
PC8.Signal=GPIO_Input
PC9.GPIO_Label=TP25
PC9.Signal=GPIO_Input
PD5.Signal=USART2_TX
PD6.Signal=USART2_RX
PE0.GPIO_Label=LED2
PE0.Signal=GPIO_Output
PE1.GPIO_Label=LED1
PE1.Signal=GPIO_Output
PF10.GPIO_Label=Sen15
PF10.Signal=ADC3_INP6
PF3.GPIO_Label=Sen22
PF3.Signal=ADC3_INP5
PF4.GPIO_Label=Sen21
PF4.Signal=ADC3_INP9
PF5.GPIO_Label=Sen20
PF5.Signal=ADC3_INP4
PF6.GPIO_Label=Sen19
PF6.Signal=ADC3_INP8
PF7.GPIO_Label=Sen18
PF7.Signal=ADC3_INP3
PF8.GPIO_Label=Sen17
PF8.Signal=ADC3_INP7
PF9.GPIO_Label=Sen16
PF9.Signal=ADC3_INP2
PG7.GPIO_Label=TP23
PG7.Signal=GPIO_Input
PG8.GPIO_Label=TP24
PG8.Signal=GPIO_Input

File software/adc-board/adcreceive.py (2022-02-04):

#!/usr/bin/env python3

# DEPRECATING THIS REAL SOON NOW
# good stuff should be moved into util.py
# and then separate tools written on top of that

import serial
import serial.tools.list_ports
import struct
import time
import threading
import atexit
from math import log10
import rtmidi
import sys
import functools
import numpy as np
import json

# try to open the right MIDI port.
midiout = rtmidi.MidiOut()
if len(midiout.get_ports())>1:
    midiout.open_port(1)
else:
    midiout.open_port(0)

# we're using the same hammer/damper pattern on both/all boards for now
hammers = [True,True,True,False,
           True,False,True,False,
           False,True,True,False,
           False,False,False,False,
           False,False,True,True,
           True,True]
# turn off any still-sounding notes.
for midinote in range(1,126):
    midiout.send_message([0x80, midinote, 64])
def vel2midi(velocity, noteon=True):
    if noteon==False and velocity>0.0:
        #print(f"prelift damper {midinote} {velocity}")
        pass
        return (0,0)
    if noteon:
        minvel = 7000.0
        maxvel = 100000.0
    else:
        minvel = -0
        maxvel = -1000
    mps = 7.5 * (velocity - minvel) / (maxvel - minvel)
    minmidivel = 1 if noteon else 32
    if mps <= 0.0001:
        midivel = minmidivel
        cc88vel = 0
    else:
        vel = 57.96 + 71.3*log10(mps)
        try:
            midivel = round(vel)
        except OverflowError:
            midivel = 0
        if midivel < minmidivel:
            #print("had low velocity", velocity, mps)
            midivel = minmidivel
            cc88vel = 0
        elif midivel > 127.0:
            midivel = 127
            cc88vel = 0
        else:
            cc88vel = round(127 * (vel % 1))
    return (midivel, cc88vel)

# this is the sensor-to-midi note pattern we're using on all channels.
#[23,27,25,25,26,24,24,23,22,21,22,21,27,26,28,29,30,31,28,29,30,31]
#[2, 6, 4, 4, 5, 3, 3, 2, 1, 0, 1, 0, 6, 5, 7, 8, 9, 10, 7, 8, 9, 10]

configuration = {
  "29002a001651393238353835": {
    # lowest notes, #4
    "channel2midi":
    [ x + 44 for x in [2, 6, 4, 4, 5, 3, 3, 2, 1, 0, 1, 0, 6, 5, 7, 8, 9, 10, 7, 8, 9, 10] ]
  },
  "2b002a001651393238353835": {
    # next lowest, #5
    "channel2midi":
    [ x + 55 for x in [2, 6, 4, 4, 5, 3, 3, 2, 1, 0, 1, 0, 6, 5, 7, 8, 9, 10, 7, 8, 9, 10] ]    
  }
}    

datafile = open("rawdata","w")

class PortHandler(object):
    def __init__(self, portname):
        self.port = serial.Serial(port=portname, baudrate=3000000, timeout=0.000001)
        self.MSGID = 0
        self.prevtime = 0
        self.timeinc = 0
        self.prevclock = 0
        self.prevnow = 0.0
        self.lock = threading.Lock()

        self.board = portname
        self.commsgood = False

        self.sendmsg(0x05)
        atexit.register(self.shutdown)
        
        self.running = True
        self.thread = threading.Thread(target=self.loop)
        self.thread.daemon = True
        self.thread.start()
        
        self.statusthread = threading.Thread(target=self.statusloop)
        self.statusthread.daemon = True
        self.statusthread.start()
        
    def statusloop(self):
        while True:
            time.sleep(30)
            self.sendmsg(0x05)

    def shutdown(self):
        self.running = False
        self.sendmsg(0x0B, struct.pack("H", 0))
        time.sleep(0.01)
        self.port.close()

    def print(self, *args):
        print(self.board, *args)

    def sendmsg(self, msgtype, body=b''):
        # keep writes and msgids, synchronized.
        # don't want to know what happens if self.port.write is
        # called simultaneously in multiple threads.
        with self.lock:
            msg = struct.pack("B", msgtype) + struct.pack("H", self.MSGID)
            self.MSGID += 1
            msg += body
            parity = 0
            for v in msg:
                parity ^= v
            msg += bytes([parity])
            newbytes = [ ]
            # escape anything that needs it
            for b in msg:
                if b in (0x7E, 0x7D):
                    newbytes.append(0x7D)
                    newbytes.append(b ^ 0x10)
                else:
                    newbytes.append(b)
                msg = bytes([0x7E] + newbytes + [0x7E])
            self.port.write(msg)

    def handle_message(self, msg):
        now = time.time()
        calcparity = 0
        for v in msg[:-1]:
            calcparity ^= v
        parity = msg[-1]

        if len(msg) < 4:
            self.print("runt frame")
            return
        msgtype = msg[0]
        msgid = struct.unpack("H", msg[1:3])[0]
        msg = msg[3:-1]
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

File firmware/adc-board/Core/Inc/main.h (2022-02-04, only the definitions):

#define Sen22_Pin GPIO_PIN_3
#define Sen22_GPIO_Port GPIOF
#define Sen21_Pin GPIO_PIN_4
#define Sen21_GPIO_Port GPIOF
#define Sen20_Pin GPIO_PIN_5
#define Sen20_GPIO_Port GPIOF
#define Sen19_Pin GPIO_PIN_6
#define Sen19_GPIO_Port GPIOF
#define Sen18_Pin GPIO_PIN_7
#define Sen18_GPIO_Port GPIOF
#define Sen17_Pin GPIO_PIN_8
#define Sen17_GPIO_Port GPIOF
#define Sen16_Pin GPIO_PIN_9
#define Sen16_GPIO_Port GPIOF
#define Sen15_Pin GPIO_PIN_10
#define Sen15_GPIO_Port GPIOF
#define Sen14_Pin GPIO_PIN_0
#define Sen14_GPIO_Port GPIOC
#define Sen13_Pin GPIO_PIN_1
#define Sen13_GPIO_Port GPIOC
#define Sen10_Pin GPIO_PIN_0
#define Sen10_GPIO_Port GPIOA
#define Sen11_Pin GPIO_PIN_1
#define Sen11_GPIO_Port GPIOA
#define Sen12_Pin GPIO_PIN_2
#define Sen12_GPIO_Port GPIOA
#define Sen9_Pin GPIO_PIN_3
#define Sen9_GPIO_Port GPIOA
#define Sen8_Pin GPIO_PIN_4
#define Sen8_GPIO_Port GPIOA
#define Sen7_Pin GPIO_PIN_5
#define Sen7_GPIO_Port GPIOA
#define Sen6_Pin GPIO_PIN_6
#define Sen6_GPIO_Port GPIOA
#define Sen5_Pin GPIO_PIN_7
#define Sen5_GPIO_Port GPIOA
#define Sen4_Pin GPIO_PIN_4
#define Sen4_GPIO_Port GPIOC
#define Sen3_Pin GPIO_PIN_5
#define Sen3_GPIO_Port GPIOC
#define Sen2_Pin GPIO_PIN_0
#define Sen2_GPIO_Port GPIOB
#define Sen1_Pin GPIO_PIN_1
#define Sen1_GPIO_Port GPIOB
#define RS485_TX_Pin GPIO_PIN_10
#define RS485_TX_GPIO_Port GPIOB
#define RS485_RX_Pin GPIO_PIN_11
#define RS485_RX_GPIO_Port GPIOB
#define TP23_Pin GPIO_PIN_7
#define TP23_GPIO_Port GPIOG
#define TP24_Pin GPIO_PIN_8
#define TP24_GPIO_Port GPIOG
#define TP28_Pin GPIO_PIN_8
#define TP28_GPIO_Port GPIOC
#define TP25_Pin GPIO_PIN_9
#define TP25_GPIO_Port GPIOC
#define TP26_Pin GPIO_PIN_8
#define TP26_GPIO_Port GPIOA
#define TP27_Pin GPIO_PIN_10
#define TP27_GPIO_Port GPIOA
#define LED4_Pin GPIO_PIN_10
#define LED4_GPIO_Port GPIOC
#define LED3_Pin GPIO_PIN_12
#define LED3_GPIO_Port GPIOC
#define LED2_Pin GPIO_PIN_0
#define LED2_GPIO_Port GPIOE
#define LED1_Pin GPIO_PIN_1
#define LED1_GPIO_Port GPIOE

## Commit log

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2020-11-02 feed phototransistors from +3.3VA. reduce reg->5V->VDDA->reg loop size.
    [ADC Board.kicad_pcb, ADC Board.sch]
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2020-11-09 protective mosfet on power input. all THT parts
    [led-power-simple.kicad_pcb, led-power-simple.sch]
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2020-11-14 correct RS485 termination resistors, adjust ground pours
    [ADC Board.kicad_pcb, ADC Board.sch, Analog Input.sch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]
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2020-11-17 first rev of reasonable new LED power board
    [led-power.kicad_pcb, led-power.sch]
2020-11-17 alternative power inputs; cap on NRST; 3.3V reg thermal work on PCB
    [ADC Board.kicad_pcb, ADC Board.sch, Analog Input.sch]
2020-11-17 include GND in power jumper header so it can receive external power
    [link-adapter.kicad_pcb, link-adapter.sch]
2020-11-17 USB VBUS sensing; rearrange/correct USARTs
    [ADC Board.kicad_pcb, ADC Board.sch]
2020-11-17 move USB ferrite closer to connector; add VCC pad near BOOT pulldown
    [ADC Board.kicad_pcb, ADC Board.sch, Analog Input.sch]
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2020-11-22 correct the jtag header
    [ADC Board.kicad_pcb, ADC Board.sch]
2020-12-03 fix missing ground in rev0; adjust silk screen for readability
    [link-adapter.kicad_pcb, link-adapter.sch]
2020-12-03 switch to STM32H743, add GPIO and missing periph, label GPIO and analog pins
    [adc-board.ioc]
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2020-12-03 Various changes from initial stages of board bringup
    * Add thermal relief to lots of connections
    * +3.3V power LED
    * BOOT0 jumper for pull to +3.3V
    * Reorder USB TVS & ferrite bead
    * Tweaking and compaction of some traces
    [ADC Board.kicad_pcb, ADC Board.sch]
2020-12-04 Lots of LED power bring-up corrections
    * MSOP-8 footprint for op amps
    * TO-220 footprint for FETs
    * Moved C10 away from J9
    * Stopped bothering with length-adjusted traces to resistors
    * Moved diodes away from LED strip terminals
    * Silkscreen tweaks
    [led-power.kicad_pcb, led-power.sch]
2020-12-06 Add a header for measuring current to ADC board
    [link-adapter.kicad_pcb, link-adapter.sch]
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2020-12-06 Significant copper pour tweaks, and packing traces in tighter
    [ADC Board.kicad_pcb]
2020-12-06 Reverse polarity diodes; Qwiic header&IO Expander
    Also includes relevant connections for the IO expander to the
    feedback nets, and /SHDN on the voltage reference.
    [led-power.kicad_pcb, led-power.sch]
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2020-12-13 Correct 5V regulator orientation and give the GND pin more thermal relief.
    Slightly rearranged the traces coming out of the MCP1501.
    [led-power.kicad_pcb, led-power.sch]
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2020-12-13 Convert pedal board over to I2C/Qwiic. Adjust mounting hole spacing.
    [pedal-board.kicad_pcb, pedal-board.sch]
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2020-12-13 Complete pedal board I2C conversion; make I2C address configurable.
    [pedal-board.kicad_pcb, pedal-board.sch]
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2020-12-13 Include a debug header for the TX/RX lines in their TTL state.
    [midi-board.kicad_pcb, midi-board.sch]
2020-12-15 Convert analog sensing over to transimpedance amplifiers
    Also switched opamps for the TSSOP14 package, and replaced the
    fancy voltage reference with a simple 2.0V regulator.
    [ADC Board.kicad_pcb, ADC Board.sch, Analog Input.sch]
2020-12-15 shrunk the sensorboard slightly, removed extra mounting hole.
    [sensorboard-1x.kicad_pcb, sensorboard-1x.sch]
2020-12-15 First possibly complete version of the main board
    [Power.sch, main-board.kicad_pcb, main-board.sch]
2020-12-16 Swap power filter caps, tighten up trace routing
    [Power.sch, main-board.kicad_pcb]
2020-12-16 convert to surface mount caps for power filtration
    [ADC Board.kicad_pcb, ADC Board.sch]
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2020-12-18 Fix swapped RS485 Z/Y pins. Add reset supervisor and 4 pin USB header.
    [ADC Board.kicad_pcb, ADC Board.sch, RS485.sch]
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2020-12-18 Swap USART1 and USART3 on RS485 connection, so that main board has bootloader access.
    [ADC Board.kicad_pcb, ADC Board.sch]
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2020-12-18 Repair some copper pour damage I did, and update notes in the schematic.
    [ADC Board.kicad_pcb, Analog Input.sch]
2020-12-18 Copper pours, and some clippable pads for the lowest voltage.
    [led-test-bar.kicad_pcb]
2020-12-18 Remove unnecessary buffer, finish up reset line(s).
    [midi-board.kicad_pcb, midi-board.sch]
2020-12-18 Second Qwiic header, semi-split analog power rail, silkscreen tweaks.
    [pedal-board.kicad_pcb, pedal-board.sch]
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2020-12-20 Include mirrored headers for the sensorboards, in case their header has to be flipped.
    [Simple.sch, Transimpedance.sch, sensorboard-tester.kicad_pcb]
2020-12-20 Made I2C address configurable to match other boards, tweaked silkscreen
    [led-power.kicad_pcb, led-power.sch]
2020-12-20 Correct RS485 Z/Y pin swap
    [main-board.kicad_pcb, main-board.sch]
2020-12-21 Fix UART and I2C pin errors. Add ETH INTRP and RXER pins.
    Various vias added, and passives packed in better around the ethernet.
    [main-board.kicad_pcb, main-board.sch]
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2020-12-21 Had the p-channel FETs in the wrong orientation, and an unnecessary resistor.
    [Power.sch, main-board.kicad_pcb]
2020-12-21 Removed some unused nets and marked the pins NC
    [main-board.kicad_pcb, main-board.sch]
2020-12-21 Moved ethernet LEDs to a single 2x3 header instead of two 1x3
    [main-board.kicad_pcb, main-board.sch]
2020-12-21 Tweak some copper pour boundaries and trace routing.
    [ADC Board.kicad_pcb]
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2021-01-16 First round of rev 1 changes. This was a complete relayout.
    * RS485 transceiver footprint fixed
    * Compressed board to 100x100mm exactly
    * Removed ethernet
    * Changed FET footprints to SOT-23
    * Swapped USB D+/D- to correct positions
    * Spaced out +5V and GND silkscreen on power input
    * Added JLCPCB order number silkscreen
    * Spaced out Qwiic headers
    * Added some more space around 3.3V regulator.
    * Slightly increased size of electrolytic caps.
    [Power.sch, main-board.kicad_pcb, main-board.sch]
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2021-01-17 First batch of ADC rev 2 changes
    * Pulled JTAG header in from the edge
    * External power header silkscreen
    * Increased most thermal relief
    * Relocated 3.3V power indicator LED
    * Increased electrolytic cap footprint
    [ADC Board.kicad_pcb, ADC Board.sch]
2021-01-17 Rev 2 changes
    * Pulldown on VREF so that ~SHDN can work
    * Voltage dividers on the rails, fed to the MCP23017 so it can detect faults
    * Increased space between Qwiic headers
    * Bring I2C bus out on 0.100" header
    * Tweaked LED positions on the left side; right seemed to be fine.
    * Converted it to a four layer board. +15V/GND/GND/+48V
    [led-power.kicad_pcb, led-power.sch]
2021-01-18 Back to the MCP1501 for Vref. Using SOT-23-6 this time.
    [ADC Board.kicad_pcb, Analog Input.sch]
2021-01-19 MIDI board Rev 1 changes
    * Standardize mounting hole spacing
    * Change 74LVC1G06 to 74LVC1G07 in schematic
    * Expose ~IRQ headers
    * Increase Qwiic header space
    * Improve TLP185(SE footprint; remove unused pads, label orientation
    * Bring I2C out on a header.
    [midi-board.kicad_pcb, midi-board.sch]
2021-01-20 Rev 1 first batch of changes
    - Made it narrower, but had to expand the space between mounting holes.
    - Moved the jacks back 2.3mm.
    - 10mm to board edge, 5mm clearance on the inside of the board, 7.5mm clearance on either side
    - Fixed the outline to be silkscreen, not a hole in the mask
    - Added I2C bus header
    - Made nice little three pad footprints for spots where you need a pull up or a pull down.
    - Drastically increased the space between the Qwiic headers
    - On the pedal jacks, the signal is really on the Tip, not the ring where I had it. Not sure what I was thinking.
    [pedal-board.kicad_pcb, pedal-board.sch]
2021-01-21 Add RTC oscillator, battery header and LDO
    Also moved the boot pin to defaulting from flash.
    [main-board.kicad_pcb, main-board.sch]
2021-01-21 Tweak some traces, and bump the board rev
    [ADC Board.kicad_pcb, midi-board.kicad_pcb, pedal-board.kicad_pcb]
2021-01-21 Add ~IRQ header, lots of trace cleanup. Bump the board rev
    [led-power.kicad_pcb, led-power.sch]
2021-01-21 Cleanup and reconcile the headers. Switch to SOT23 regulators for both.
    [Simple.sch, Transimpedance.sch, sensorboard-tester.kicad_pcb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]
2021-01-21 Tweak a bunch of traces, bump the board rev
    [main-board.kicad_pcb, main-board.sch]
2021-02-28 rearranged sensorboard stuff in prep for multiple sensor boards
    [simple-1x.kicad_pcb, simple-1x.sch]
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2022-01-20 Fix ADC configuration issues
    Also migrate CubeMX configuration to a new version
    [adc-board.ioc, main.c, main.h]
2022-01-21 ADC Board to Kicad 6; made corrections for updated DRC & ERC.
    [ADC Board.kicad_pcb, ADC Board.kicad_sch, ADC Board.sch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]
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2022-01-24 Including some OpenSCAD files for 3D printed parts I've used.
    [back-block.scad, cny70-protector.scad, lr-block.scad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]
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2022-01-30 Built about half of automatic calibration.
    Fixed a bug in HDLC processing.
    Started splitting the python script out into different programs.
    [calibratekey.py, calibrator.py, hdlc.c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]
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2022-02-02 Update 4x boards for issue #44; introduce the 12deg rotated hammer board
    [2020-centered-4x-12deg.kicad_pcb, 2020-centered-4x-12deg.kicad_sch, 2020-centered-4x-12deg.sch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]
2022-02-04 Made issue #44 changes to sensorboards, introduced 3x versions
    Also finished bringing them up to Kicad 6.0
    [2020-offset-1x.kicad_pcb, 2020-offset-1x.kicad_sch, 2020-offset-2x.kicad_pcb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]
2022-02-04 Include the USB LED power board, for completeness sake.
    [usb-led-power.kicad_pcb, usb-led-power.kicad_sch]
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2022-02-04 Include some files which had been omitted previously.
    [mounting_plate.scad]
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2022-02-13 Unified ground nets in schematic and layout.
    * Rearranged the layers that pours are on.
    * Added the keep-out zone separating analog and
    digital areas from each other.
    * Tightened up placement of decoupling capacitors.
    [ADC Board.kicad_pcb, ADC Board.kicad_sch, Analog Input.kicad_sch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]
2022-02-14 LED power board improvements, per issue #42
    * Increased thermal relief
    * Moved C10 well away from J9
    * R24 and R9 are now the same value, 3.6kohm
    * Removed R0
    * Removed the need for the +15V supply with an LM317.
    * Removed I2C IO expander and replaced with an STM32G0
    [led-power.kicad_pcb, led-power.kicad_sch]
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2022-02-16 Made most changes for rev 2 of MIDI board
    * Silkscreen for I2C header
    * Converted from specialized I2C UART to an STM32G0
    * Replace the specialized 74-series open-drain buffer with a BJT
    * Switch to using a BJT to pull down the interrupt line.
    [midi-board.kicad_pcb, midi-board.kicad_sch, midi-board.sch]
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2022-02-16 Made changes for pedal board rev 2, per issue #40
    * 1uF caps on all the incoming signal lines
    * Switched to STM32G0 from the I2C ADC
    * Added IRQ support, with transistor for pull down
    * Every TRS pin is brought to an ADC pin, so we can attempt autodetection
    of pedal behavior.
    [pedal-board.kicad_pcb, pedal-board.kicad_sch, pedal-board.sch]
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2022-02-16 More ADC board rev 3 changes, per issue #47
    * 4.5V regulator for phototransistors
    * new 3.3V regulator for analog section
    * new 2.0V precision voltage reference
    * Analog voltages and their distribution rearranged
    * Tidied up traces on the left hand side, everything is nice and curvy now
    * Adjusted USB ESD protection to be optional and/or support other parts
    [ADC Board.kicad_pcb, ADC Board.kicad_sch, Analog Input.kicad_sch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]
2022-02-17 Brought out all ADC lines, and put some power on adjacent pins
    [pedal-board.kicad_pcb, pedal-board.kicad_sch]
2022-02-20 main board changes for rev 2 per issue #41
    * Added a bit more thermal relief to everything on the top layer
    * Looked at the RS485 and I2C caps thermal relief and called it good enough.
    * Fixed silkscreen of C20 and most everything else, as I upgraded to KiCad 6 footprints and the refs all moved.
    * Changed the ferrite bead footprint to the handsoldering one.
    * Tweaked the specified values for the Pwr and Stat LEDs, but not much.
    * Removed battery connector and associated bits.
    * That left remove to move over the JTAG header.
    * Switched to using the SDMMC peripheral for accessing the SD card.
    * Had SDCARD_DET net attached to the wrong side of the pull up; fixed.
    * Made all of the high speed tr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
    [Power.kicad_sch, main-board.kicad_pcb, main-board.kicad_sch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]
2022-02-22 ADC board layout tweaks; rearranged the various power planes
    * Moved to standard plane layout of power, ground, ground, power,
    which I should've done from the start.
    * Removed pads from the mounting holes, don't want to risk ground
    loops through the frame, there's no value.
    * Adjusted the position of the 3.3VA regulator.
    * Tweaked/tightened up a lot of traces, trying to keep them shorter.
    * Bunch of extra vias stitching planes together.
    [ADC Board.kicad_pcb, ADC Board.kicad_sch]
2022-02-24 Removing CubeMX file for main board that used the wrong processor.
    [main-board.ioc]
2022-02-24 Correct CubeMX file for the main board brought in
    Re-double checked it against the schematic, including the SDMMC interface
    [main-board.ioc]
2022-02-25 Convert all other mounting holes to non-pad variety.
    Reroute a few traces to be shorter.
    [led-power.kicad_pcb, led-power.kicad_sch, main-board.kicad_pcb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]
2022-04-24 Next revs of the important boards
    Includes some tiny DRC tweaks for the LED power board.
    [ADC Board.kicad_pcb, Power.kicad_sch, led-power.kicad_pcb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]
2022-04-25 Correct name for the 2040-centered-4x-12deg board
    [2020-centered-4x-12deg.sch, 2040-centered-4x-12deg.kicad_pcb, 2040-centered-4x-12deg.kicad_sch]
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2022-06-05 HDLC layer uses UART DMA for transmit, per issue #51
    [adc-board.ioc, hdlc.c, main.c]
2022-06-05 Fix bug in HDLC DMA transmit for issue #51
    [hdlc.c]

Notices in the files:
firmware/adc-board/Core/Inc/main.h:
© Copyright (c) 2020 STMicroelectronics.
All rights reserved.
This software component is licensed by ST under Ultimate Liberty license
